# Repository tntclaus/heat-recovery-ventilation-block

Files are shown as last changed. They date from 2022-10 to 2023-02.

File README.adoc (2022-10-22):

= Комнатный рекуператор

Комнатный рекуператор для установки под подоконник, на или в стену, под потолок и любые другие подходящие места.

Изготавливается из следующих материалов:

1. Комплект деталей, распечатанных на 3д принтере, включая переходники для подсоединения к воздуховоду
1. Алюминиевые трубки диаметром ø10мм с толщиной стенки 1мм
1. Клейкая теплоизоляция
1. Канальные вентиляторы способные создать достаточную тягу
1. Устройство для управления

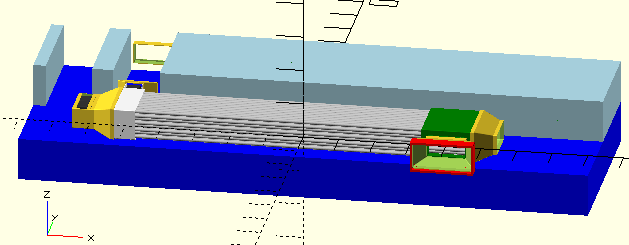
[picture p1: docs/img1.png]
3D модель теплообменника


Воздуховод изготавливается из стандартных вентканалов 110х55 или ø100. Для производительности 60 м3 / ч этого будет достаточно.

Сопротивление теплообменника со 100 трубками длинной 1м составляет порядка 40 Паскаль на вдув и 30 — на выдув.

== Фотографии

Собранный рекуператор может выглядеть так:

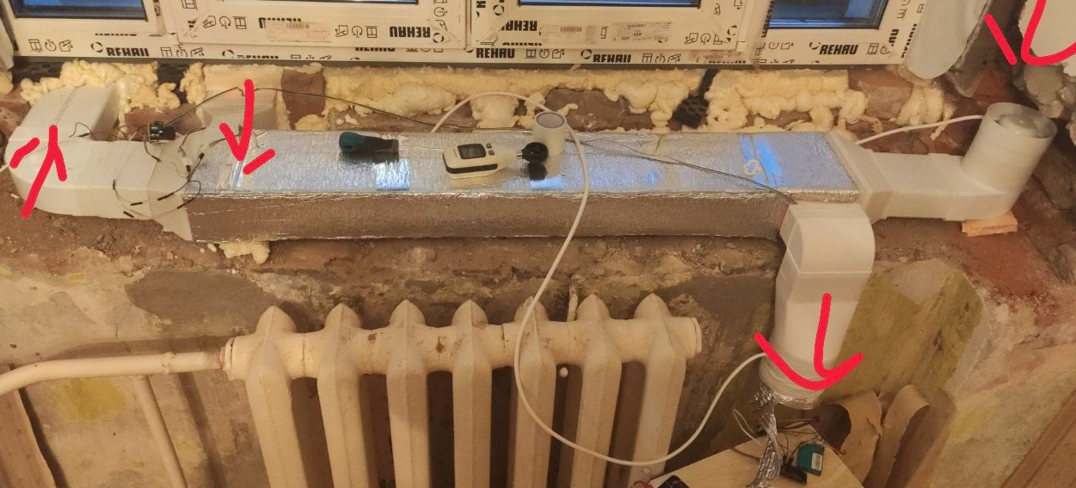
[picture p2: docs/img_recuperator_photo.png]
Фото рекуператора в сборе


== Как сгенерировать 3д модели

Весь проект создан на `OpenSCAD 2021` с использованием библиотеки NopSCADlib.

1. Склонируйте репозиторий
1. Установите OpenSCAD
1. Установите библиотеку NopSCADlib в директорию где OpenSCAD ищет библиотеки.
1. Выполните скрипт `bom.py` и затем `stl.py` из библиотеки `NopSCADlib`.

== Как собирать теплообменник

Некоторые детали генерируются 2 частями и их необходимо склеить. Выбирайте клей по вкусу, отлично подходит АБС-клей на основе ацетона. Необходимо обработать клеем или герметиком все стыки и щели для предотвращения утечек воздуха, иначе можно получить неожиданные результаты в плане .

=== Версия 0.2 (156мм х 82мм)

Тестовая версия, для продува предполагалось использовать 4 серверных вентилятора 40х28. Очень шумно и очень производительно. Для эксплуатации в комнате не подходит.

Детали теплообменника:

1. Трубки: 100 х Aluminium tube 1000x10x1
1. Картриджи для трубок: 2 х ABS_recuperator_tubes_cartridge_156x82
1. Тройники на краях теплообменника:
    - 1 х ABS_square_vent_channel_t_joint_bottom_half_w15x40x10_154x80_42x80_154x80
    - 1 х ABS_square_vent_channel_t_joint_bottom_half_w20x20x20_154x80_103x49_154x80
    - 1 х ABS_square_vent_channel_t_joint_top_half_cut_w15x40x10_154x80_42x80_154x80
    - 1 х ABS_square_vent_channel_t_joint_top_half_w20x20x20_154x80_103x49_154x80
1. Другие детали предназначены для установки сменных фильтров и вентиляторов

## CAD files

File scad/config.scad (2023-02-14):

include <NopSCADlib/vitamins/screws.scad>

use <recuperation_section.scad>

fan40x28 = [40,  28, 37, 16,    M3_dome_screw, 25,   7.5,100, 9, 0,   undef];
//fan40x28 = [40,  28, 38, 16,    M2_5_dome_screw, 25,   7.5,100, 9, 0,   undef];
fan60x20 = [60,  20, 57, 25,    M4_dome_screw, 31.5, 3.6, 64, 7, 0,   63];

fan92x25 = [92,  25, 88, 41,    M4_dome_screw, 41,   4.3, 90, 7, 0,   100];



WINDOW_WIDTH = 1600;
WINDOW_DEPTH = 300;
WINDOW_HEIGTH = 120;
AVAILABLE_DEPTH = 550;

WIDTH_O = 110;
//WIDTH_O = 204;
HEIGTH_O = 60;

WIDTH_I = WIDTH_O - 4;
HEIGTH_I = HEIGTH_O - 3;


PRINTED_WALL_THICKNESS = 2;
FAN_TYPE = fan92x25;

heatexchanger_face_type = square_vent140x100_t_joint;

inlet_width = floor(SPACE_IN(heatexchanger_face_type) / (VC(heatexchanger_face_type) * TUBE_V_SPACING()));

RECUPERATOR_IN_CHANNEL = [
    "inlet_tube_type",
    "inlet tube type",
        inlet_width,
        square_vent_channel_heigth(heatexchanger_face_type),
        inlet_width-4,
        square_vent_channel_heigth(heatexchanger_face_type)-4,
        1
    ];

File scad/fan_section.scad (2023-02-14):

include <NopSCADlib/utils/core/core.scad>
include <NopSCADlib/utils/core/rounded_rectangle.scad>

include <NopSCADlib/vitamins/nuts.scad>
include <NopSCADlib/vitamins/screws.scad>
include <NopSCADlib/vitamins/fans.scad>

include <square_vent_channels.scad>

include <config.scad>

h = 100;


module place_fans4square_vent(w) {
    translate([w/2, 0, 0])
        children();

    translate([- w/2, 0, 0])
        children();
}

function fan_to_vent(fan_type) = ["", "", fan_width(fan_type)+4, fan_width(fan_type)+4, fan_width(fan_type), fan_width(fan_type), 5];

/**
* Заглушка на канал
*/
module fan_holder_square_vent(fan_type, vent_type) {
    circular_vent92 = fan_to_vent(fan_type);

//    name = str(
//        "ABS_fan_holder_square_vent_",
//        square_vent_channel_fun_name(vent_type), "_2_fan",
//        fan_width(fan_type),"x",fan_width(fan_type)
//        );
//    stl(name);

    translate_z(-5){
        translate_z(- 26)
        fan4square_vent_cap(fan_type);

        square_vent_channel_adaptor(vent_type, circular_vent92, 30, expand = 5, stl = false);
    }
}

module fan4square_vent204x60_middle(type, length) {
    wall_thickness = PRINTED_WALL_THICKNESS;

    w_o = square_vent_channel_width(type) + wall_thickness * 2;
    h_o = square_vent_channel_heigth(type) + wall_thickness * 2;
    w = square_vent_channel_width(type);
    h = square_vent_channel_heigth(type);

    stl(str(
    "ABS_fan4square_vent204x60_middle_", square_vent_channel_fun_name(type), "_",
    "l", length));

    difference() {
        rounded_cube_xy([w_o, h_o, length], r = 2, xy_center = true, z_center = true);
        rounded_cube_xy([w, h, length * 2], r = 2, xy_center = true, z_center = true);

        translate([0, h, 0])
            cube([w, h * 2, length], center = true);
    }
}

module fan4square_vent_cap(fan_type, fan_cuts = true) {
    fw = fan_width(fan_type);
//    if(material != "") {
//        stl(str(
//        material, "_fan_cap_",
//        fan_width(fan_type), "x", fan_depth(fan_type)
//        ));
//    }

    module fan_cut(a) {
        rotate([0, 0, a])
                    rounded_cube_xy(
                        [fan_aperture(fan_type) + fan_thickness(fan_type) * 2, 4, 10],
                    1, xy_center = true, z_center = true);
    }

    module fan_base() {
        difference() {
            rounded_cube_xy([fw,fw,2], 2, xy_center = true);
            fan_holes(fan_type);
            if(fan_cuts) {
                fan_cut(45);
                fan_cut(-45);
            }
        }
    }

    translate_z(6)
    fan_base();
}

module fan4square_vent_base(fan_type, vent_type) {
    stl(str("ABS_fan4",square_vent_channel_fun_name(vent_type),"_base_fan", fan_width(fan_type), "x", fan_depth(fan_type)));

    w = fan_width(fan_type);
    module fan_base() {
        difference() {
            square_vent_channel_cube(square_vent204x60, 10);

            place_fans4square_vent(65){
                fan_holes(fan_type);
            }

            translate_z(5 + .1)
            place_fans4square_vent(65){
                fan_hole_positions(fan_type) {
                    translate_z(- fan_depth(fan_type) / 2)
                    vflip()
                    cylinder(r = nut_radius(M4_nut), h = nut_trap_depth(M4_nut), $fn = 6);
                }
            }
        }
    }

    fan_base();
}

module fan_inblower_assembly(vent_type, fan_type) {
    w = fan_width(fan_type)+1;

    assembly("fan_inblower") {
        translate_z(-40)
        fan(fan_type);
        fan_holder_square_vent(fan_type,change_type(vent_type, 9, 9));
        translate_z(-33)
        color("red")
        FLEX_fan_gasket_stl();
    }
}

module fan_outblower_assembly() {
    fan_type = FAN_TYPE;
    w = fan_width(fan_type);

    assembly("fan_outblower") {
        translate_z(-30.5)
        fan(fan_type);
        ABS_airduct_outlet_fan_adaptor_stl();

        translate_z(-24)
        color("red")
        FLEX_fan_gasket_stl();

        translate_z(-62)
        FLEX_outlet_fan_2_tube_adaptor_stl();
        translate_z(-80) {
            ABS_fan_sleeve_stl();
            hflip() vflip() ABS_fan_sleeve_stl();
        }
    }
}



module ABS_fan_sleeve_stl() {
    stl("ABS_fan_sleeve");
    fw = fan_width(FAN_TYPE) + 10;
    fw_inner = fan_width(FAN_TYPE) + 4;

    module place_mount_hole() {
        for(x = [-1, 1])
        translate([x*(fw/2+6),0,0])
            rotate([90,0,0])
                children();
    }

    translate_z(40)
    difference() {
        union() {
            rounded_cube_xy([fw, fw, 10], 2, xy_center = true, z_center = true);
            rounded_cube_xz([fw_inner+30, 7, 10], 2, xy_center = true, z_center = true);


        }
        rounded_cube_xy([fw_inner, fw_inner, 11], 2, xy_center = true, z_center = true);

        translate([0,fw-.25,0])
        cube([fw*2,fw*2,fw*2], center = true);

        place_mount_hole()
            cylinder(d = 3.5, h = 100, center = true);
    }


    //    cube([fw,fw,fw]);
}

//module ABS_fan4square_vent_cap_fan60x20_stl() {
//    fan4square_vent_cap(fan60x20);
//}
//
//module ABS_fan4square_vent204x60_middle_square_vent_204x60_l30_stl() {
//    fan4square_vent204x60_middle(square_vent204x60, 30);
//}
//
//module ABS_fan4square_vent_base_fan60x20_stl() {
//    fan4square_vent_base(fan60x20);
//}

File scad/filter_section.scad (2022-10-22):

include <NopSCADlib/utils/core/core.scad>

include <square_vent_channels.scad>
include <config.scad>
use <sections.scad>


/**
* Фильтр из металлической сетки:
* Mesh 60 или 30 — https://aliexpress.ru/item/1005003473125481.html
*/
module mesh_filter(type) {
    stl(str("ABS_mesh_filter_cap_", square_vent_channel_fun_name(type)));

    length = 20;
    wall_thickness = PRINTED_WALL_THICKNESS;
    channel_cap_model(type, wall_thickness, length);
}

/**
* Деталь для установки фильтров, склеивается из 3 частей.
* Подключается между двух плоских воздуховодов.
*/
module air_filter_holder_assembly(type) {
    assembly("air_filter_holder") {
        d = 42;
        translate_z(d / 2)
        air_filter_holder_side(type);

        translate_z(- d / 2)
        rotate([180, 0, 0])
            air_filter_holder_side(type);

        air_filter_holder_middle(type, length = 32);
    }
}


module air_filter_heat_breaker_assembly(type, l = 8) {
    assembly("air_filter_holder") {
        d = l;
        translate_z(d / 2)
        air_filter_holder_side(type);

        translate_z(- d / 2)
        rotate([180, 0, 0])
            air_filter_holder_side(type);

        air_filter_holder_middle(type, length = l);
    }
}

/**
* Многослойный фильтр:
* Слой 1 ( 5мм) — грубая очистка https://aliexpress.ru/item/32760571194.html
* Слой 2 (10мм) — HEPA https://aliexpress.ru/item/1005001619559275.html
* Слой 3 ( 5мм) — угольный фильтр https://aliexpress.ru/item/32789944517.html
* Толщина 20 мм
*/
module air_filter_cassette_assembly(type) {
    inside_type = inside_type(square_vent110x55);

    air_filter_cassette_top(inside_type);
    vflip()
    air_filter_cassette_bottom(inside_type);
}

module air_filter_cassette_top(type) {
    stl(str("ABS_air_filter_cassette_top_", square_vent_channel_fun_name(type)));
    channel_cap_model(type, PRINTED_WALL_THICKNESS, 31.8);
}

module air_filter_cassette_bottom(type) {
    stl(str("ABS_air_filter_cassette_bottom_", square_vent_channel_fun_name(type)));

    translate_z(-31.8/2+7.5/2)
    square_vent_channel_model(type, 5);
}


module air_filter_holder_side(type) {
    stl(str("ABS_air_filter_holder_side_", square_vent_channel_fun_name(type)));

    length = 10;
    wall_thickness = PRINTED_WALL_THICKNESS;
    channel_cap_model(type, wall_thickness, length);
}

module air_filter_holder_middle(type, length) {
    wall_thickness = PRINTED_WALL_THICKNESS;

    w_o = square_vent_channel_width(type) + wall_thickness * 2;
    h_o = square_vent_channel_heigth(type) + wall_thickness * 2;
    w = square_vent_channel_width(type);
    h = square_vent_channel_heigth(type);

    stl(str(
    "ABS_air_filter_holder_middle_", square_vent_channel_fun_name(type), "_",
    "l", length));

    difference() {
        rounded_cube_xy([w_o, h_o, length], r = 2, xy_center = true, z_center = true);
        rounded_cube_xy([w, h, length*2], r = 2, xy_center = true, z_center = true);

        translate([0,h,0])
        cube([w, h*2, length], center = true);
    }
}


/***
 ***
 *** Генераторы STL
 ***
 ***/
module ABS_air_filter_holder_middle_square_vent_110x55_l32_stl() {
    air_filter_holder_middle(square_vent110x55, length = 32);
}

module ABS_air_filter_holder_side_square_vent_110x55_stl() {
    air_filter_holder_side(square_vent110x55);
}


module ABS_mesh_filter_cap_square_vent_110x55_stl() {
    mesh_filter(square_vent110x55);
}

module ABS_air_filter_cassette_top_square_vent_105x50_stl() {
    type = square_vent110x55;
    inside_type = inside_type(square_vent110x55);
    air_filter_cassette_top(inside_type);
}


module ABS_air_filter_cassette_bottom_square_vent_105x50_stl(){
    type = square_vent110x55;
    inside_type = inside_type(square_vent110x55);
    air_filter_cassette_bottom(inside_type);
}

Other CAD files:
scad/main.scad
scad/recuperation_section.scad
scad/sections.scad
scad/square_vent_channel.scad
scad/square_vent_channels.scad
scad/under_window.scad
scad/valve_section.scad

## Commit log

2022-09-02 блоки для фильтров блок теплообменника
    [config.scad, fan_section.scad, filter_section.scad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]
2022-09-03 кассета для сборного фильтра
    [fan_section.scad, filter_section.scad, main.scad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]
2022-09-03 секция заслонки
    [filter_section.scad, main.scad, sections.scad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]
2022-09-04 секция кастомизируемого тройника
    [sections.scad, square_vent_channel.scad, square_vent_channels.scad]
2022-09-07 адаптор двух сечений и тройники
    [fan_section.scad, main.scad, recuperation_section.scad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]
2022-09-10 адаптор для фильтра
    [fan_section.scad, main.scad, square_vent_channel.scad]
2022-09-11 адапторы для вдува и выдува
    [main.scad, sections.scad, square_vent_channels.scad]
2022-10-22 рекуператор: версия 1
    [fan_section.scad, filter_section.scad, main.scad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]
2022-10-22 описание версии 0.2
2022-10-22 переходники с теплообменника на круглую трубу D100
    [main.scad, sections.scad, square_vent_channel.scad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]
2022-10-22 исправлена толщина адаптора
    [square_vent_channels.scad]
2023-02-02 заменены вентиляторы, добавлены гибкие рукава-гармошки
    [fan_section.scad, main.scad, recuperation_section.scad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]
2023-02-02 гибкие рукава-гармошки для квадратных переходных адаптеров
    [main.scad, square_vent_channel.scad]
2023-02-14 исследование по распределению углекислого газа в помещениях
2023-02-14 гибкие переходники, манжеты вокруг гибких переходников
    [config.scad, fan_section.scad, main.scad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]
2023-09-30 труба с карманами для шумоизоляции
    [main.scad, square_vent_channels.scad]
